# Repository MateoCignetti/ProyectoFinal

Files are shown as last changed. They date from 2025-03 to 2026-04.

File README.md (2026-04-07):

## Repositorio para el proyecto final de la carrera Ingeniería Electrónica. UTN FR San Francisco, 2025.

# Autores
- [ ] Alesandria, Alejo
- [ ] Cignetti, Mateo Antonio
- [ ] Galliano, Ignacio

Shield: [][cc-by-nc-sa]

Esta obra está bajo una
[Licencia Creative Commons Atribución-NoComercial-CompartirIgual 4.0 Internacional][cc-by-nc-sa].

[][cc-by-nc-sa]

[cc-by-nc-sa]: https://creativecommons.org/licenses/by-nc-sa/4.0/deed.es
[cc-by-nc-sa-image]: https://licensebuttons.net/l/by-nc-sa/4.0/88x31.png
[cc-by-nc-sa-shield]: https://img.shields.io/badge/License-CC%20BY--NC--SA%204.0-lightgrey.svg

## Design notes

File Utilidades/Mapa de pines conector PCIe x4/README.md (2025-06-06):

# Tabla de Pines ESP32-S3 para el conector PCIe x4

| Símbolo PCIe x4 | Pad Footprint PCIe x4 | GPIO ESP32-S3 |
|:---:|:---:|:---:|
| HP_Power | 1 | 35 |
| AGND | 7 | GND |
|  3,3Vdc_Signal  | 8 | 3V3 |
| S1 | 9 | 4 (ADC1_3)  |
| S2 | 10 | 5 (ADC1_4)  |
| S3 | 11 | 6 (ADC1_5)  |
| S4 | 12 | 7 (ADC1_6)  |
| S5 | 13 |  15 (ADC2_4)  |
| S6 | 14 |  16 (ADC2_5)  |
| S7 | 15 |  17 (ADC2_6)  |
| S8 | 16 |  18 (ADC2_7)  |
| S9 | 17 | 8 (ADC1_7)  |
| S10 | 18 | 36 |
| S11 | 19 | 37 |
| S12 | 20 | 38 |
| S13 | 21 | 39 |
| S14 | 22 | 40 |
| S15 | 23 | 41 |
| S16 | 24 | 2 (ADC1_1)  |
| MODULE_IDENT  | 25 | 3 (ADC1_0)  |
| HP_Signal | 26 | 42 |

# Imágenes de referencia

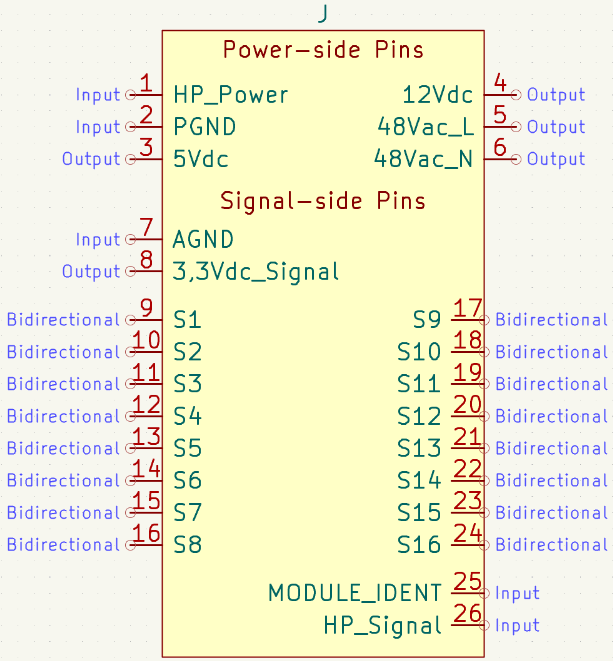
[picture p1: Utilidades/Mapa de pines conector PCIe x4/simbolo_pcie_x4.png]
simbolo-pcie


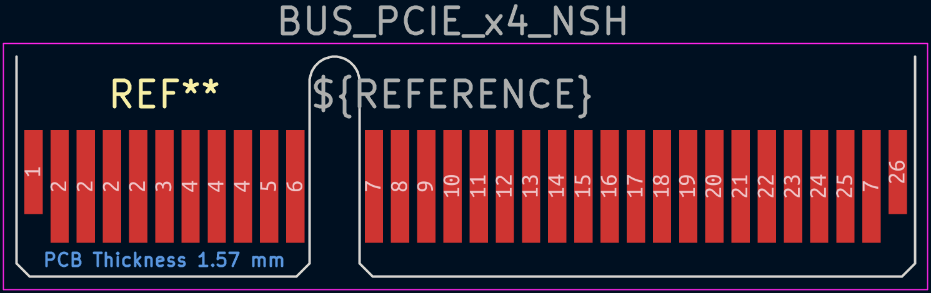
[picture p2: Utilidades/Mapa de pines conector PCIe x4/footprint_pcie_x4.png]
footprint-pcie


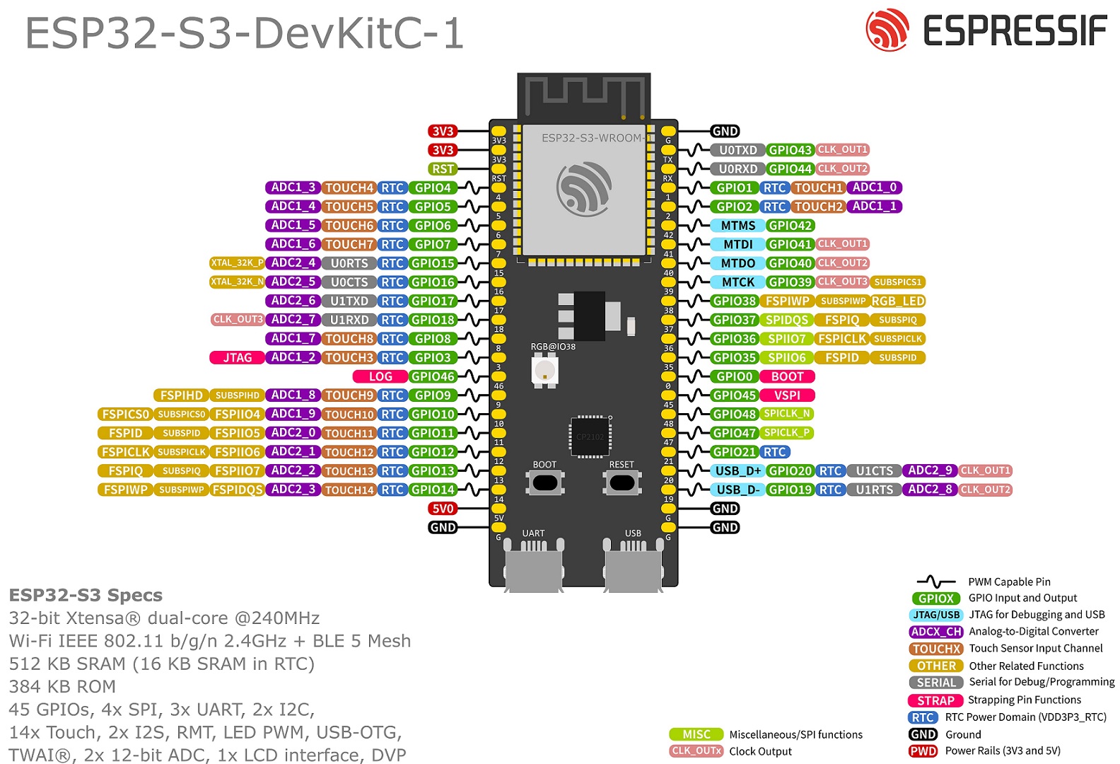
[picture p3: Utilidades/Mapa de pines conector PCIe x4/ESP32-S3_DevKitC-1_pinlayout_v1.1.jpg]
pinout-esp32


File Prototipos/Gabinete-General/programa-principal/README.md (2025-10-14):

| Supported Targets | ESP32-S3 |
| --- | --- |

# General Cabinet - Main Control Program

Modular control system for the General Cabinet project. Automatically detects and manages hot-pluggable power electronics modules.

## Adding New Modules

**Quick Start:** See [MODULE_TEMPLATE.md](MODULE_TEMPLATE.md) for a complete guide.

**Summary:** To add a new module, you only need to:
1. Create `your_module.h` in `modules_include/`
2. Create `your_module.c` in `modules_src/`
3. Edit `module_registry.h` only (add include + list entry)

**Zero changes to core manager code!** See [MODULE_TEMPLATE.md](MODULE_TEMPLATE.md).

(See the README.md file in the upper level 'examples' directory for more information about examples.)

## How to use example

Follow detailed instructions provided specifically for this example.

Select the instructions depending on Espressif chip installed on your development board:

- [ESP32 Getting Started Guide](https://docs.espressif.com/projects/esp-idf/en/stable/get-started/index.html)
- [ESP32-S2 Getting Started Guide](https://docs.espressif.com/projects/esp-idf/en/latest/esp32s2/get-started/index.html)

## Example folder contents

The project **hello_world** contains one source file in C language [hello_world_main.c](main/hello_world_main.c). The file is located in folder [main](main).

ESP-IDF projects are built using CMake. The project build configuration is contained in `CMakeLists.txt` files that provide set of directives and instructions describing the project's source files and targets (executable, library, or both).

Below is short explanation of remaining files in the project folder.

```
├── CMakeLists.txt
├── pytest_hello_world.py      Python script used for automated testing
├── main
│   ├── CMakeLists.txt
│   └── hello_world_main.c
└── README.md                  This is the file you are currently reading
```

For more information on structure and contents of ESP-IDF projects, please refer to Section [Build System](https://docs.espressif.com/projects/esp-idf/en/latest/esp32/api-guides/build-system.html) of the ESP-IDF Programming Guide.

## Troubleshooting

* Program upload failure

    * Hardware connection is not correct: run `idf.py -p PORT monitor`, and reboot your board to see if there are any output logs.
    * The baud rate for downloading is too high: lower your baud rate in the `menuconfig` menu, and try again.

## Technical support and feedback

Please use the following feedback channels:

* For technical queries, go to the [esp32.com](https://esp32.com/) forum
* For a feature request or bug report, create a [GitHub issue](https://github.com/espressif/esp-idf/issues)

We will get back to you as soon as possible.

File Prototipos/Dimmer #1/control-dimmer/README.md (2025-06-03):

# English:
| Supported Targets | ESP32-S3 |
| --- | --- |

## Control for the Dimmer #1 Prototype

This firmware controls the Dimmer #1 prototype using an ESP32-S3 microcontroller. It detects zero crossings of the AC signal and uses two hardware timers to precisely control a TRIAC for phase-cut dimming. The dimming level is set via an analog input (ADC), and all timing is handled without blocking the main program. The code includes optional test signal generation for development without real AC hardware. All configuration and control logic is implemented in `main.c`.

# Español:
| Dispositivos Soportados | ESP32-S3 |
| --- | --- |

## Control para el Prototipo Dimmer #1

Este firmware controla el prototipo Dimmer #1 utilizando un microcontrolador ESP32-S3. Detecta los cruces por cero de la señal de CA y utiliza dos temporizadores de hardware para controlar con precisión un TRIAC mediante atenuación por corte de fase. El nivel de atenuación se ajusta mediante una entrada analógica (ADC), y toda la temporización se gestiona sin bloquear el programa principal. El código incluye la generación opcional de señales de prueba para el desarrollo sin hardware de CA real. Toda la configuración y lógica de control está implementada en `main.c`.

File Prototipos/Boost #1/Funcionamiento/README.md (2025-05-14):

# Convertidor Boost

Circuito genérico del convertidor Boost

### Lista de Entradas-Salidas

<!-- 
| Señal | Tipo |
|----|-----|
| Tensión de alimentación | Entrada |
| Señal de control gate | Entrada |
| Tensión de salida | Salida |
| Tensión de retroalimentación | Salida |
-->

| Entrada | Salida |
|----|-----|
| Tensión de alimentación, $V_{cc}$ = 12 V | Tensión de salida, $V_{out}$ = 24 V|
| Señal de control gate, PWM -- 0 a 3,3 V | Tensión de retroalimentación, $V_\beta$ entre 0 y 3,3 V  |

El desarrollo siguiente fue obtenido de, [Electrical Technology](https://www.electricaltechnology.org/2020/09/buck-converter.html), 

## Resumen
Un convertidor boost, también conocido como elevador de voltaje, es un tipo de convertidor DC-DC que incrementa la tensión de entrada a un nivel superior en la salida. Funciona almacenando energía en un inductor durante el tiempo en que un interruptor (generalmente un transistor) está cerrado, y transfiriéndola a través de un diodo hacia la carga cuando el interruptor se abre. 

Este aumento de tensión en la salida se consigue a expensas de una menor corriente de salida. Aunque esto depende del diseño específico, es común que la corriente disminuya al elevar el voltaje, de manera de conservar la potencia según el principio de conservación de la energía.
<!--
FALTA HACER RESUMEN
-->

## Funcionamiento

### Componentes principales del convertidor

* Interruptor, puede ser un transistor BJT como un MOSFET.
* Diodo de rectificación.
* Inductor.
* Capacitor de salida.
* Controlador PWM.

### Modo Encendido

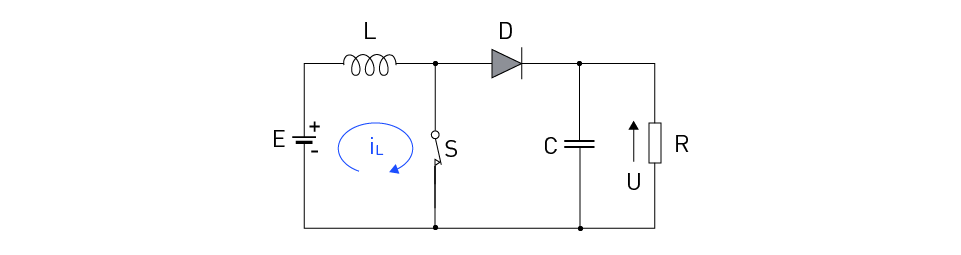
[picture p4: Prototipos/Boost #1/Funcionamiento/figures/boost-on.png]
Modo 1


Durante esta etapa, el voltaje de entrada es aplicado al inductor, generando que acumule energía. El diodo se encuentra polarizado inversamente debido a que el nodo que se encuentra entre el inductor, interruptor y el diodo, se encuentra a un potencial prácticamente de 0, por ello la corriente se deriva por el interruptor y no por el diodo, además hay que considerar que en esta etapa, el capacitor de salida se encuentra suministrando energía a la carga, por ende el cátodo del diodo se encuentra a un potencial mayor que el ánodo del mismo, por eso se dice que está polarizado de forma inversa.

### Modo Apagado

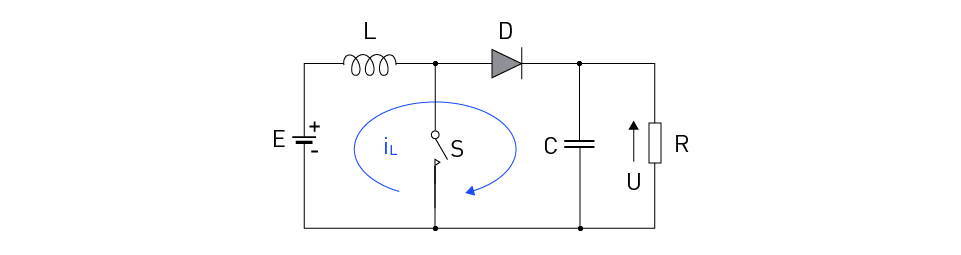
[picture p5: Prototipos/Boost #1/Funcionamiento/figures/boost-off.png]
Modo 2


Cuando el interruptor se abre, toda la energía almacenada en el inductor es aplicada en el diodo haciendo que el mismo se polarice directamente, produciendo que el inductor disminuya la energía almacenada en el mismo. 

### Medición de tensión

La medición de tensión se realiza de la misma forma que en el caso del convertidor Buck, en caso de ser necesario una mayor explicación retomar el documento, FUNCIONAMIENTO DEL BUCK

Si el interruptor tiene un período de conmutación lo suficientemente rápido, el inductor no llega a descargase en su totalidad entre los períodos, haciendo que en la carga se aplique un voltaje mayor al voltaje de entrada. También, mientras el interruptor está abierto, el capacitor de salida se carga con este voltaje combinado. Cuando el interruptor se cierra, el capacitor de salida es el encargado de suministrar energía a la carga. Por ello el interruptor debe ser rápidamente conmutado a abierto para evitar la descarga completa del capacitor de salida.

$V_{out} = \frac{V_{in}}{1-D}$

La ecuación anterior muestra el voltaje en régimen permanente, y como al aumentar el duty, la tensión de salida se ve aumentada.

### Modo continuo y descontinuo de conducción

**Modo Continuo de conducción**

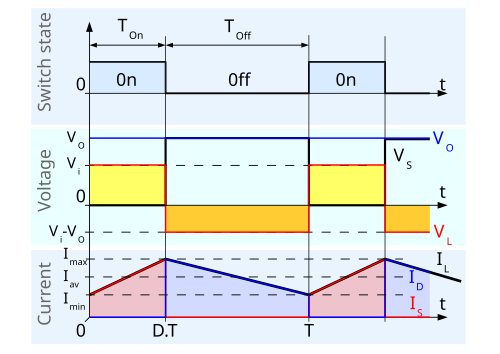
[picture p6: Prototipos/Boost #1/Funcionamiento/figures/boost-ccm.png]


**Modo Discontinuo de conducción**

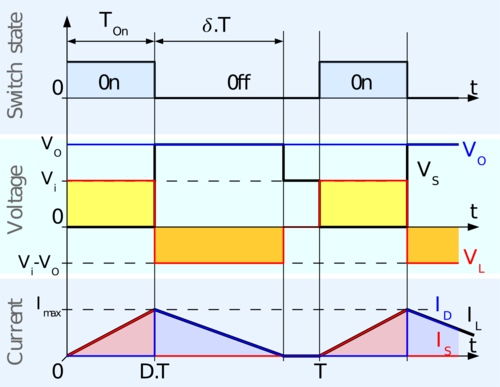
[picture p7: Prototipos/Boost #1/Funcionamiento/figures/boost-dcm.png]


Para cargas ligeras, el convertidor trabaja en modo Discontinuo.

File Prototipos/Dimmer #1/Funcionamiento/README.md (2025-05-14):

# Recortador de onda "Dimmer"

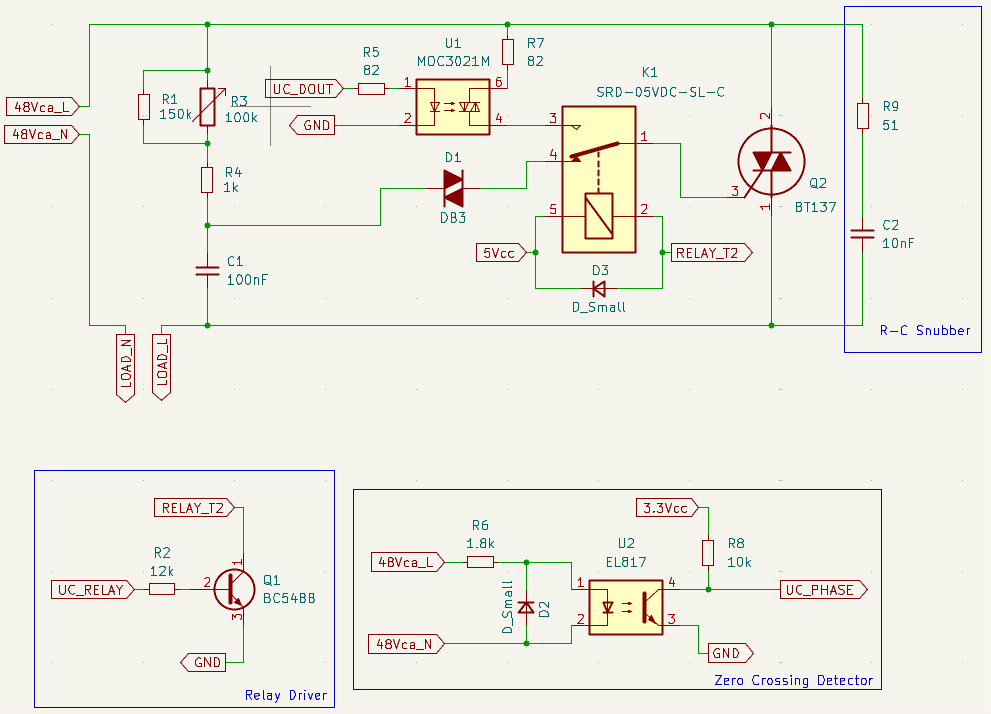
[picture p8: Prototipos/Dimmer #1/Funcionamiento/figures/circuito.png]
Circuito de placa Dimmer


## Entradas y salidas
| Entrada | Salida |
|--- |--- |
|$V_{ca}$ = 48 Vca | $UC_{phase}$ = Onda cuadrada 3.3 Vcc  |
|$5V_{cc}$ = 5 Vcc | $Load$ = Onda recortada 0-48 Vca RMS  |
|$3.3V_{cc}$ = 3.3 Vcc | |
|$UC_{Dout}$ = Pulso 3.3 Vcc | |
|$UC_{Relay}$ = 0 V o 3.3 Vcc | |

## Resumen

El recortador de onda "Dimmer" tiene como objetivo regular la potencia
entregada a la carga, mediante el uso de un tiristor, recortando la onda
de tensión aplicada a la carga. En esta placa, se utilizan dos métodos
distintos de control: analógico y digital.

El control analógico permite cambiar el ángulo de disparo del tiristor TRIAC. Con un simple circuito R-C, se varía la resistencia y, por lo tanto, la constante de tiempo de carga del capacitor para retardar el disparo del DIAC, encargado de disparar el TRIAC. Debido al comportamiento del TRIAC, una vez "disparado", no deja de conducir hasta el cruce por cero de la tensión aplicada entre ambos ánodos.

El control digital se compone de dos circuitos distintos: el Zero Crossing Detector (detector de cruce por cero) y el driver de TRIAC. El primero permite al microcontrolador sincronizarse con la tensión de corriente alterna y el segundo permite al microcontrolador "disparar" el TRIAC cuando se quiera.

Con un circuito driver de Relé, se permite cambiar entre ambos modos, siendo el control analógico el activado por defecto (contacto normal-cerrado).

## Control de fase con tiristores

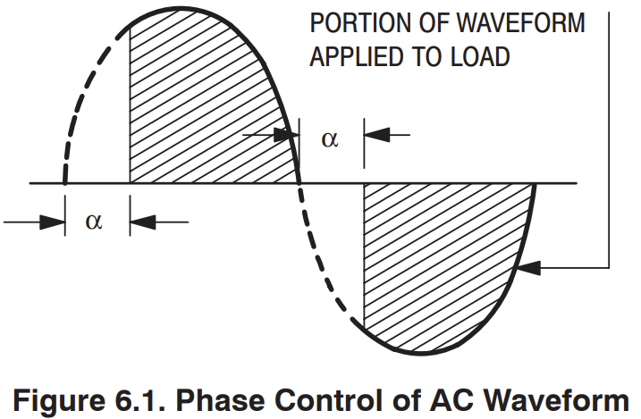
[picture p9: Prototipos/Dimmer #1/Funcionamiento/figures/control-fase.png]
Control de fase


El método más común de control electrónico de potencia de CA se denomina control de fase. La Figura 6.1 ilustra este concepto. Durante la primera parte de cada semiciclo de la onda sinusoidal de CA, se abre un interruptor electrónico para impedir el flujo de corriente. En un ángulo de fase específico $\alpha$, este interruptor se cierra para permitir que se aplique toda la tensión de línea a la carga durante el resto de ese semiciclo. La variación de $\alpha$ controlará la parte de la onda sinusoidal total que se aplica a la carga (área sombreada) y, por lo tanto, regulará el flujo de potencia hacia la carga.

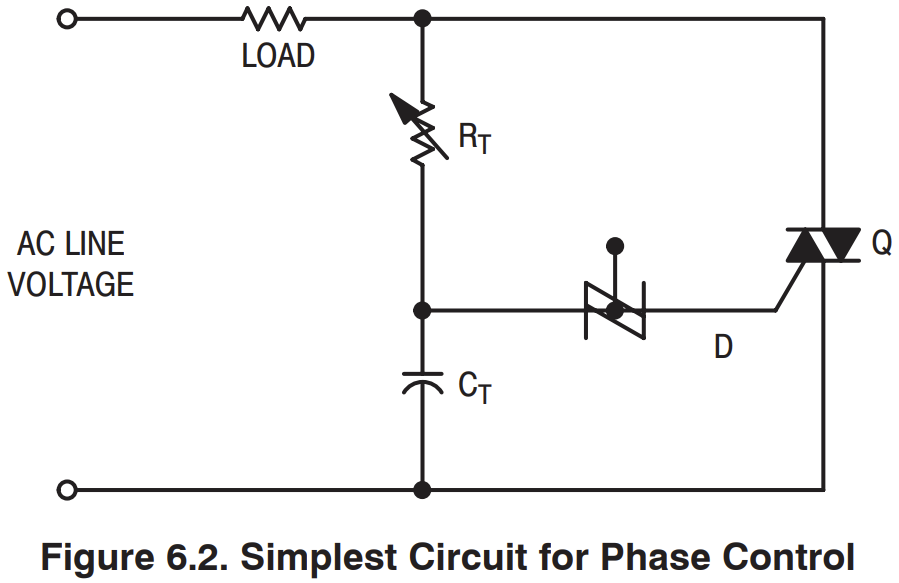
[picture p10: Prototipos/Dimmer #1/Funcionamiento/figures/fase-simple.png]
Circuito básico de control de fase


El circuito más simple para lograr el control de fase se muestra en la Figura 6.2. En este caso, el interruptor electrónico es un TRIAC (Q) que se activa mediante un pequeño pulso de corriente en su compuerta. El TRIAC se desactiva automáticamente cuando la corriente que lo atraviesa pasa por cero. En el circuito mostrado, el capacitor CT se carga durante cada semiciclo mediante la corriente que fluye a través de la resistencia RT y la carga. El hecho de que la carga esté en serie con RT durante esta parte del ciclo tiene poca importancia, ya que la resistencia de RT es mucho mayor que la de la carga. Cuando la tensión en el CT alcanza la tensión de ruptura del disparador bilateral DIAC (D), se libera la energía almacenada en el capacitor CT. Esta energía produce un pulso de corriente en el DIAC, que fluye a través de la compuerta del TRIAC y lo activa. Dado que tanto el DIAC como el TRIAC son dispositivos bidireccionales, los valores de RT y CT determinarán el ángulo de fase en el que se activará el TRIAC en los semiciclos positivo y negativo de la onda sinusoidal de CA.

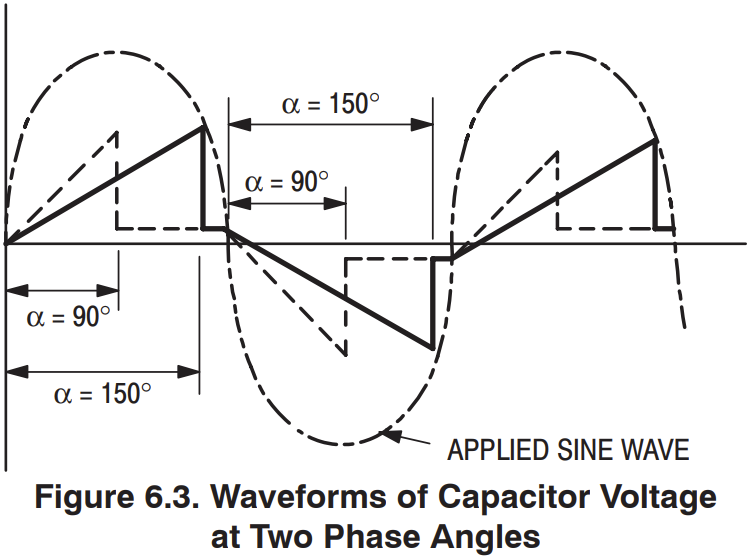
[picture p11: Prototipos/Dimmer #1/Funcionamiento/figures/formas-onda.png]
Formas de onda de tensión de capacitor


La forma de onda del voltaje a través del capacitor para dos condiciones de control típicas ($\alpha$ = 90° y 150°) se muestra en la Figura 6.3. Si se utiliza un rectificador controlado por silicio en este circuito en lugar del TRIAC, solo se controlará un semiciclo de la forma de onda. El otro semiciclo se bloqueará, lo que genera una salida de CC pulsante cuyo valor promedio puede variarse ajustando el RT. 
(Referencia: [Thyristor Theory and Design Considerations: Handbook](https://www.rsp-italy.it/Electronics/Databooks/ON/_contents/ON%20Thyristor%20theory%20and%20design%20handbook%20HBD855D%202005.pdf))

Este tipo de control de fase se recomienda solamente para circuitos con carga resistiva o levemente inductiva (ver [AN308 (STMicroelectronics)](https://www.st.com/resource/en/application_note/an308-triac-analog-control-circuits-for-inductive-loads-stmicroelectronics.pdf))

## Circuito detector de cruce por cero (ZCD)

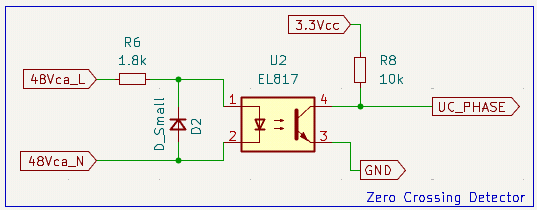
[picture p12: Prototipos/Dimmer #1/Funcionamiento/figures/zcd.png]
Circuito ZCD


Este simple circuito convierte la señal de entrada de CA sinusoidal en una señal aislada cuadrada, que permite al microcontrolador conocer el momento de cruce por cero (cuando la onda cuadrada pasa de 3,3 V a 0 V o 0 V a 3,3 V).

En el semiciclo positivo de la tensión de CA, se enciende el led interno del optoacoplador, lo que polariza el transistor de salida, que lleva la tensión UC_PHASE a 0 V. En el semiciclo negativo, la corriente fluye por el diodo D2, manteniendo la tensión reversa del led interno fija y menor a la máxima permitida (6 V para el EL817).

## Driver de TRIAC

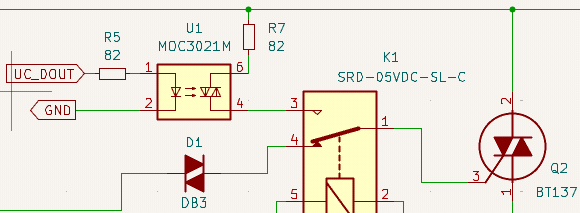
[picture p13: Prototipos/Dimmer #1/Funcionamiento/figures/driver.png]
Driver TRIAC


Con este circuito se permite disparar el TRIAC en cualquier momento de forma aislada, solamente enviando un pulso con el microcontrolador a UC_DOUT. No es necesario mantener la señal por más que unos pocos microsegundos, ya que una vez disparado el TRIAC, no deja de conducir hasta que la tensión aplicada entre ambos ánodos cruza por cero.

## Driver de relé

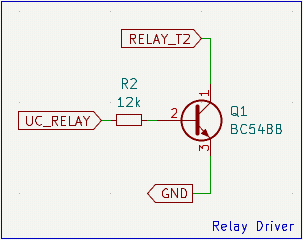
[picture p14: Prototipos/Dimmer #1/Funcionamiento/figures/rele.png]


Simple circuito que permite conmutar el relé, para así cambiar entre ambos modos de control (analógico y digital). Cuando UC_RELAY es de 0 V, el circuito utilizado es el de control analógico, mientras que cuando UC_RELAY es de 3,3 V, se activa el control digital.

## Red Snubber

Es imperativo implementar algún método para restringir la tasa de aumento de la tensión reaplicada del triac a un valor que permita la desactivación del triac en condiciones de carga inductiva. Un método comúnmente aceptado para mantener la dv/dt de conmutación dentro de niveles tolerables es utilizar una red Snubber RC en paralelo con los terminales principales del triac. Dado que la tasa de aumento de la tensión aplicada en los terminales del triac depende de la impedancia de carga y de la red Snubber RC, el circuito puede evaluarse en las peores condiciones de temperatura de funcionamiento y corriente principal máxima. Los valores de resistencia y capacitancia en red Snubber se ajustan entonces para que la tasa de aumento de la tensión dv/dt de conmutación se encuentre dentro del límite mínimo especificado en cualquiera de las condiciones mencionadas anteriormente. El valor de la resistencia del Snubber debe ser lo suficientemente alto como para limitar las corrientes de descarga de la capacitancia del Snubber durante el encendido y amortiguar la oscilación del LC durante la conmutación. Generalmente, se prefiere la combinación de valores de Snubber con la mayor resistencia y la menor capacitancia que proporcione un funcionamiento satisfactorio. (Referencia: [Thyristor Theory and Design Considerations: Handbook](https://www.rsp-italy.it/Electronics/Databooks/ON/_contents/ON%20Thyristor%20theory%20and%20design%20handbook%20HBD855D%202005.pdf))

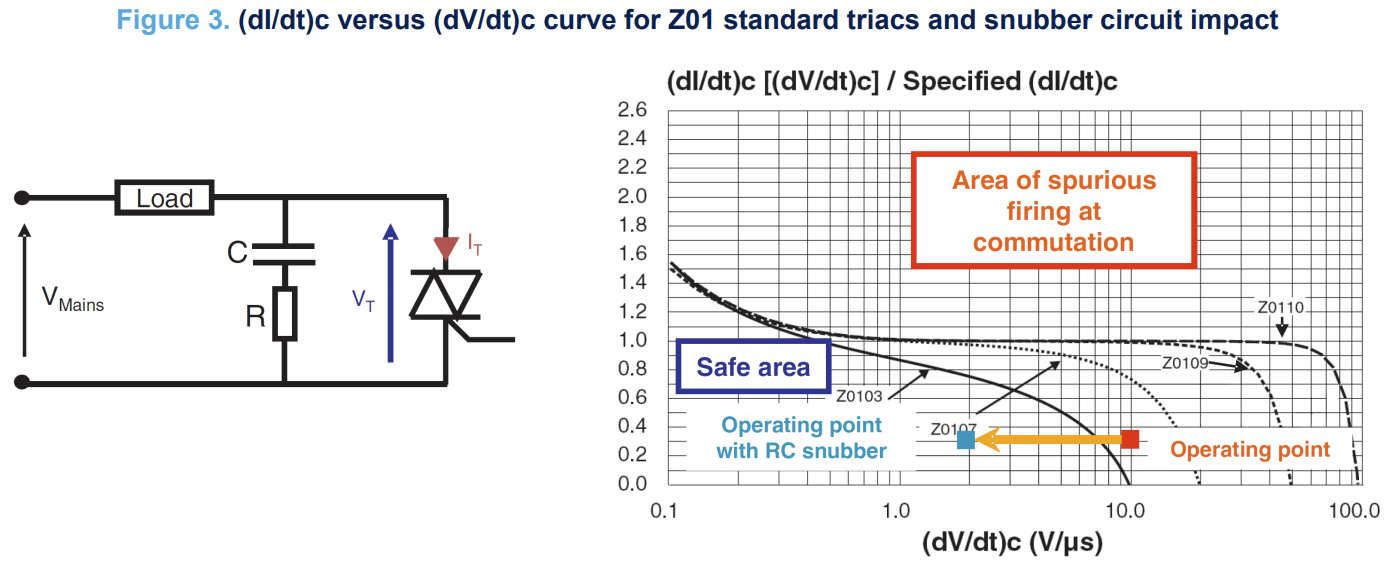
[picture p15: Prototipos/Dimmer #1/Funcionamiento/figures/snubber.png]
Red Snubber


Como se observa en la figura 3, un alto dv/dt puede causar un falso disparo del TRIAC, afectando negativamente al circuito control de fase. (Más info, ver [AN437 STMicroelectronics](https://www.st.com/resource/en/application_note/an437-rc-snubber-circuit-design-for-triacs-stmicroelectronics.pdf))

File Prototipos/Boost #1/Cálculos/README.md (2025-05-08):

# Diseño de Convertidor Boost

Circuito Boost

### Requisitos

| Entrada | Salida |
|- |- |
|$V_{in}$ = 12 V |$V_{out}$ = 24 V |
|$I_{in}$ = 1 A |$I_{out}$ = 0,5 A  |

El diseño del convertidor fue realizado siguiendo el siguiente documento, [Texas Instruments](https://www.ti.com/lit/an/slva372d/slva372d.pdf?ts=1743949048852)

**Criterios de diseño del circuito**

* $R_{load} = \frac{24 V}{0,5 A} = 48 \Omega$
* Ripple,
  * $\Delta I_L = I_{in} * 0,3 = 1  A * 0,3 = 0,3 \ A$
  * $\Delta V_{out} = V_{out} * 0,05 = 1,2 \ V$
* Frecuencia de conmutación, 15 kHz.

## Cálculo del Duty Cycle máximo

$$D = 1 - \frac{V_{in} * \eta }{V_{out}} = 1 - \frac{12 * 0,8 }{24} = 0,6$$

## Cálculo de Inductor

$$L = \frac{V_{in} * (V_{out} - V_{in})}{\Delta I_L * f_s * V_{out}} = \frac{12V * (24V - 12V)}{0,3A * 15 \times 10^3 Hz * 24V} = 1,33 mH$$

Tal vez sea conveniente la elección de un inductor arbitrario y luego calcular el ripple producto del mismo. Se deja como inquietud para las pruebas prácticas. Este valor se verá afectado en función de la fuente que se utilice para alimentación, 1 A tal vez es poca corriente. Si la corriente de entrada es de 2 A, el inductor se reduce a la mitad 666,66 uH

## Selección de Capacitor de entrada

Utilizado para filtrar la tensión de entrada, si la fuente es demasiado ruidosa, el capacitor se puede incrementar para mejorar el filtrado. 

Valor elegido, $1 \ \mu F$. Requerirá ajustes en la práctica.

## Cálculo de Capacitor de salida

$$C_{out} = \frac{I_{out} * D}{f_s * \Delta V_{out}} = \frac{0,5 A * 0,6}{15 \times 10^3 Hz * 1,2 V} = 16,67 \ \mu F$$

## Cálculo de corriente por el diodo

$$I_D = I_{out_{max}}$$

Se recomienda el uso de diodos Schottky.

## Red de realimentación

$$V_{out} = \frac{V_{in}*R_2}{R_1+R_2}$$

$$3,3 V= \frac{24 V * 4,7 k\Omega}{R_1 + 4,7 k\Omega}$$

$$R_1 = 29,48 k\Omega \approx 27 k\Omega + 2,2 k\Omega$$

## Cálculo red Snubber transistor de conmutación

Para más detalles sobre el cálculo revisar, [Cáculos Buck](https://github.com/MateoCignetti/ProyectoFinal/tree/main/Prototipos/Buck%20%231/C%C3%A1lculos). Además los transistores utilizados como driver son los mismos, por ende la red de Snubber también lo es (se tendrá que comprobar en la práctica).

Se supone un valor de inductancia parásita típico de 50 nH. $C_P = C_{OSS}$

* IRFZ44N

$C_{OSS} = 330 pF = C_{snub_{min}}$

$$f_{ring} = \frac{1}{2 \pi * \sqrt{L_P * C_P}} = \frac{1}{2 \pi * \sqrt{50 \ nH * 330 \ pF}} = 39,18 \ MHz$$

$$ R_{snub} = \frac{1}{2\pi f_{ring} C_{snub}} = 12,31 \ \Omega$$

## Filtro RC para entrada de ADC

$f_c = 100 Hz$

$C = 1 \ \mu F$

$f_c = \frac{1}{2\pi * R * C}$

$$R = \frac{1}{2\pi * f_c * C} = 1591 \ \Omega \approx 1,5  \ k\Omega$$

## Diseño Prototipo Boost 12 V a 24 V

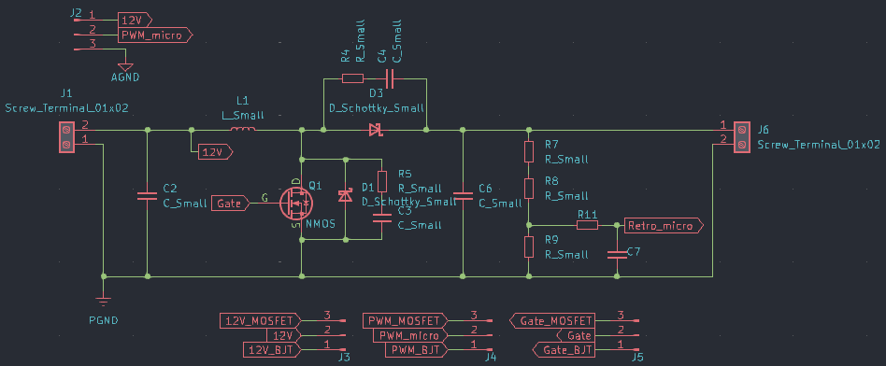
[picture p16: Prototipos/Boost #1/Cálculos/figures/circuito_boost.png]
Circuito Boost

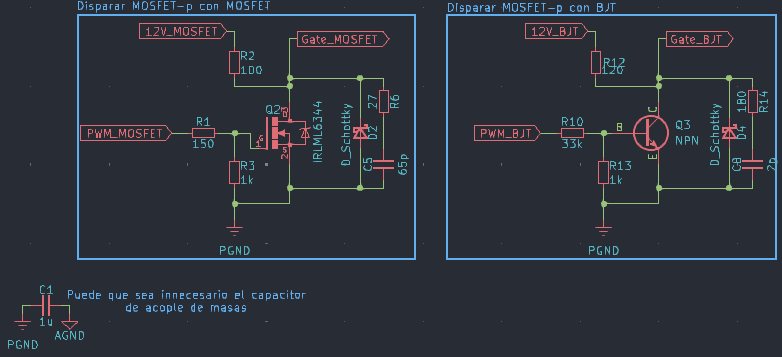
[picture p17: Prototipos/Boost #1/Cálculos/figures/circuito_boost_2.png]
Circuito Boost


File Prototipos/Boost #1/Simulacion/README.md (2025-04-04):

# Resultados de Simulación

## Circuito Convertidor Boost

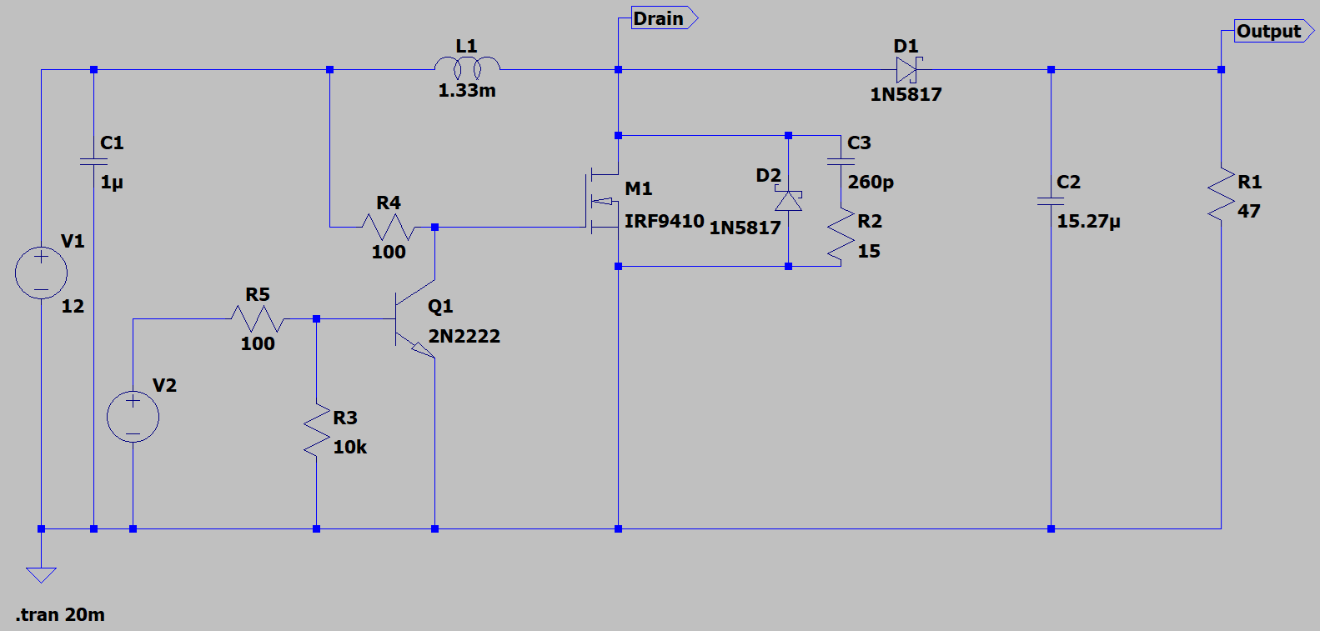
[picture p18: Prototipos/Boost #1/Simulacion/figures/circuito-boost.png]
Convertidor Boost


### Tensión de Salida del convertidor

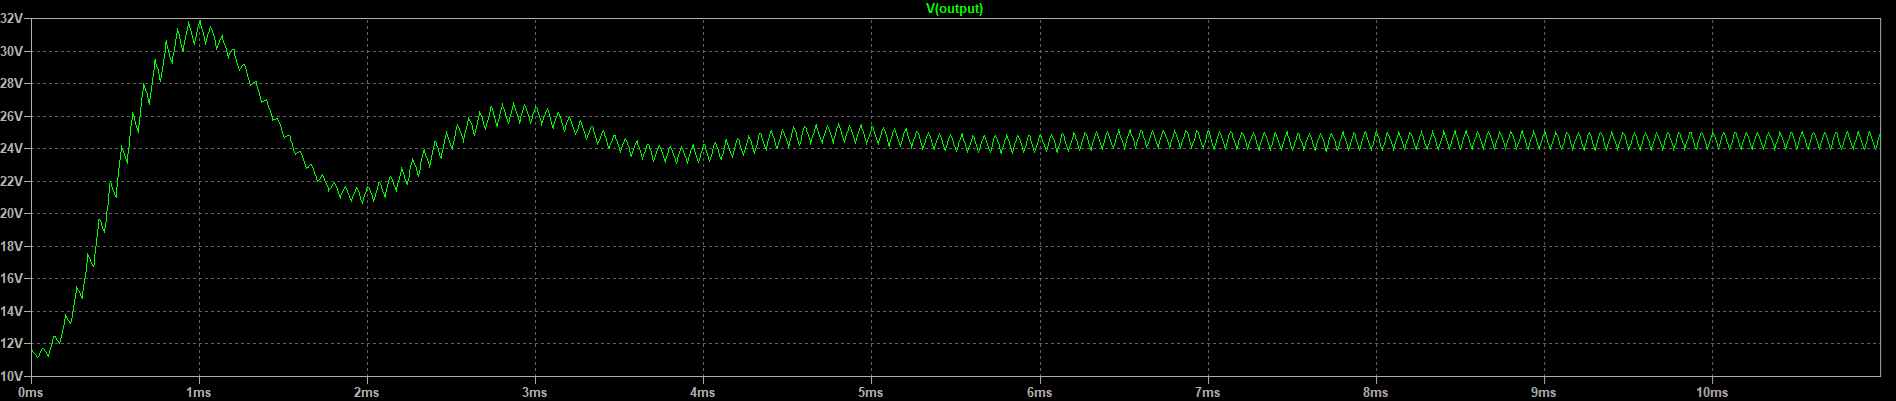
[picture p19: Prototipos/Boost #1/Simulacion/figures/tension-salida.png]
Convertidor Boost


La tensión de salida de convertidor presenta una respuesta subamortiguada por la naturaleza de un sistema
de segundo orden. Para mejorar la respuesta del convertidor es necesario un sistema de control sencillo, como
puede ser un PI.

### Modo CCM

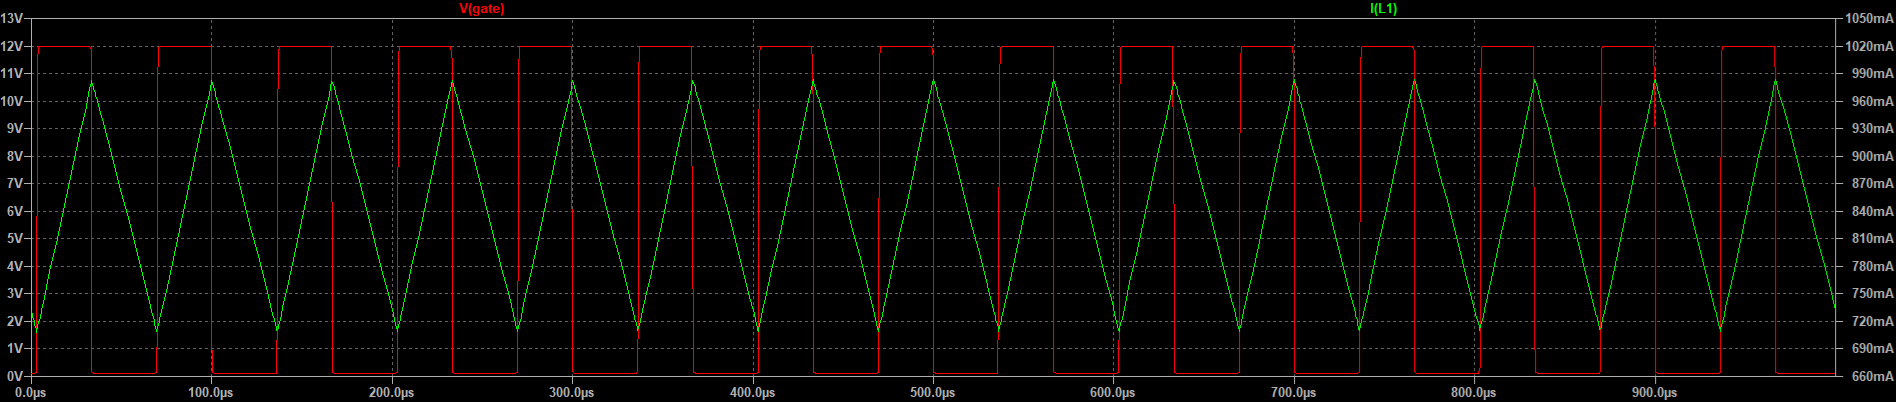
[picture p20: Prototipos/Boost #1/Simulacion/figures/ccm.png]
Convertidor Boost


La corriente en el inductor nunca llega a ser '0' por ello se lo denomina modo continuo de conducción. 
Suele ser necesario cuando la carga requiere más corriente.

Pruebas con carga de 47 $\Omega$ y un duty de 44 %

### Modo DCM

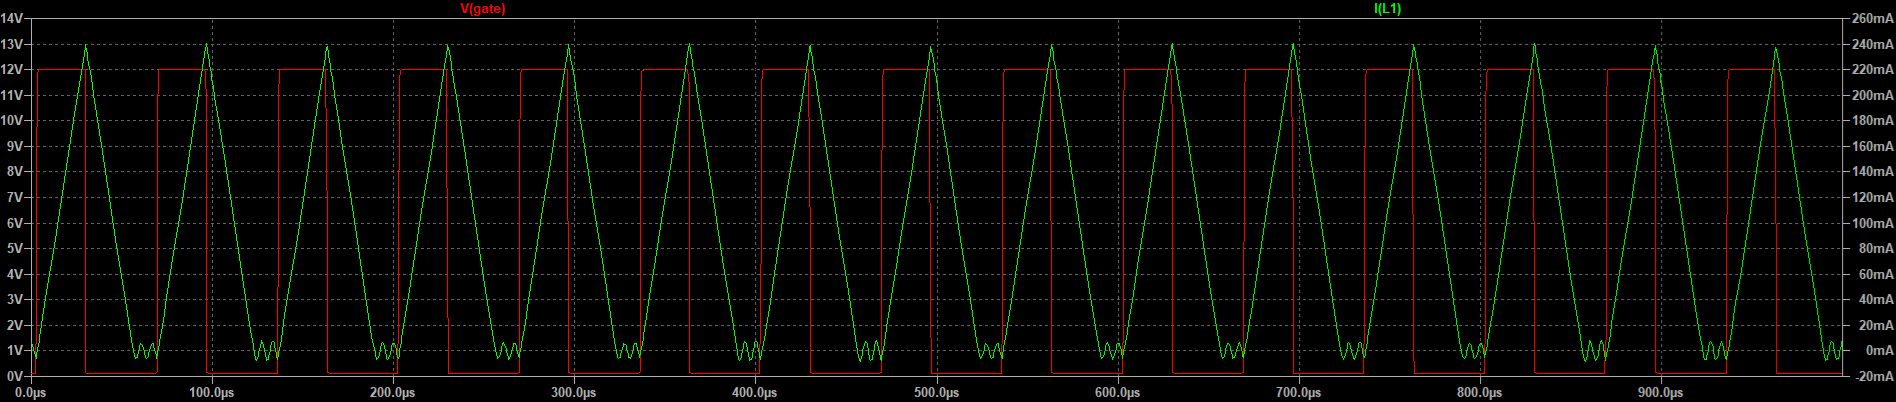
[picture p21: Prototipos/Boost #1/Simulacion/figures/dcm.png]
Convertidor Boost


En este caso, a diferencia del CCM, la corriente en el inductor es '0' antes de que el transistor de conmutación se encienda nuevamente. Este modo se lo conoce como modo discontinuo de conducción. Se aplica
cuando la carga no tiene un consumo excesivo.

Pruebas con carga de 400 $\Omega$ y un duty de 39 %

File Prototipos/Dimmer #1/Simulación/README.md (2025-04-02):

# Resultados simulación

## Circuito
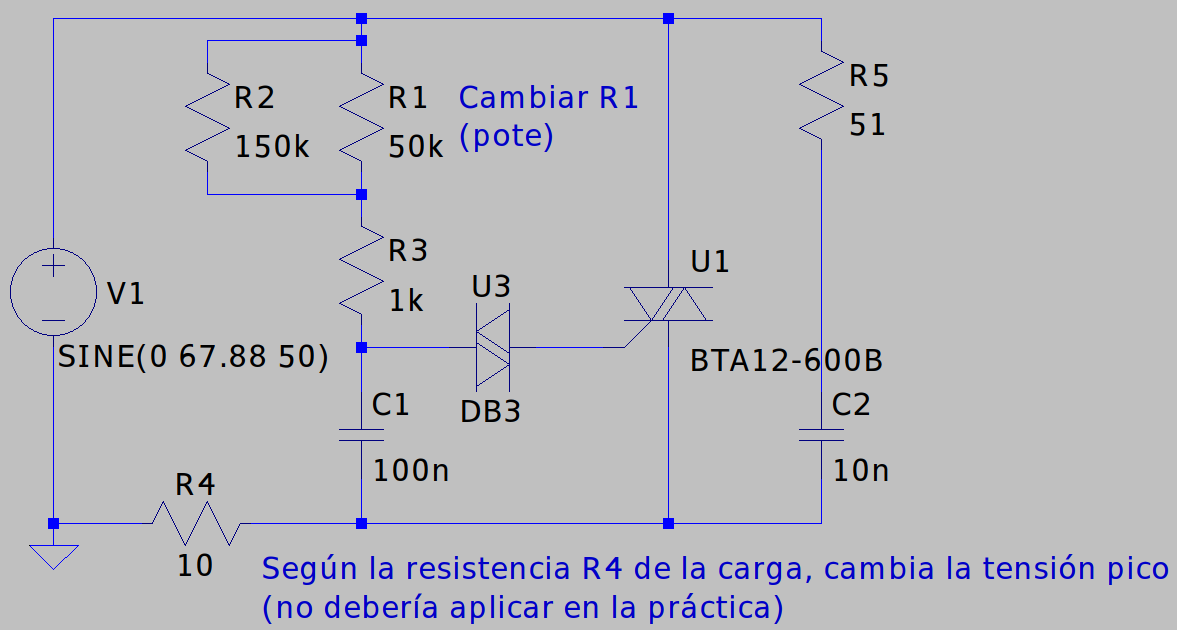
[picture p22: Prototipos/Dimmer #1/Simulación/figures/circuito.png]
Circuito


## Formas de onda
- 🔵 Tensión de entrada
- 🟢 Tensión en la carga

(La amplitud varía según el valor de la resistencia de la carga, en la práctica no debería afectar)

### Potenciómetro en 0
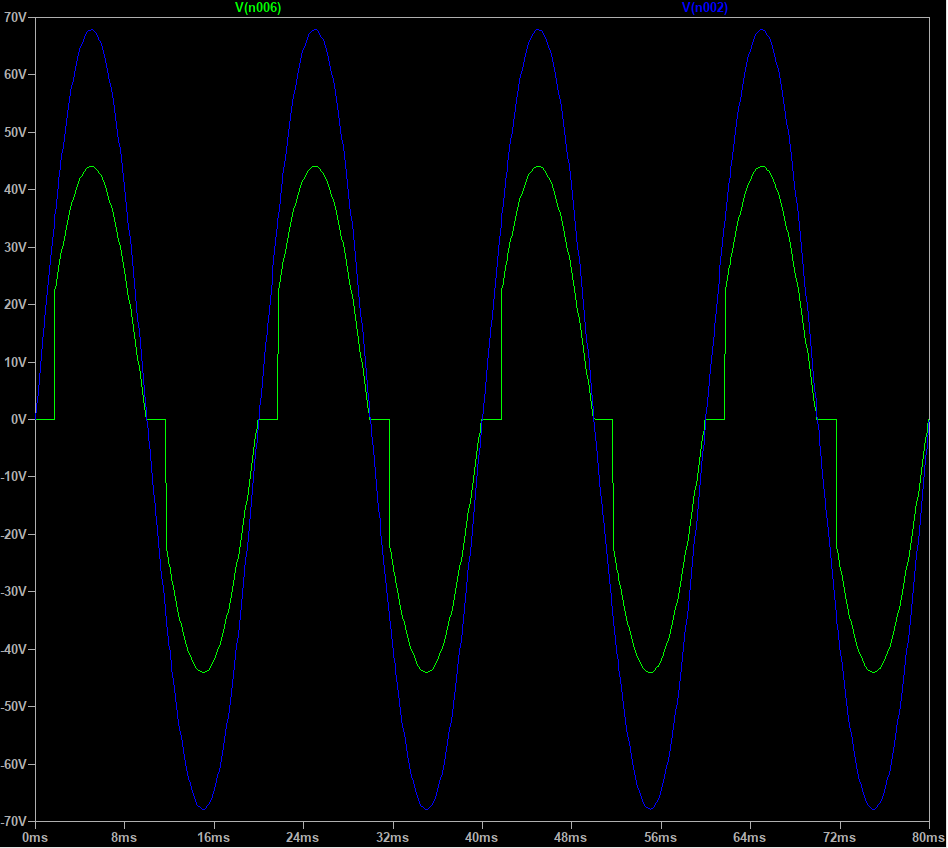
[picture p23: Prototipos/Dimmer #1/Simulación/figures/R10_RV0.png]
Pote0


### Potenciómetro en 50k (50%)
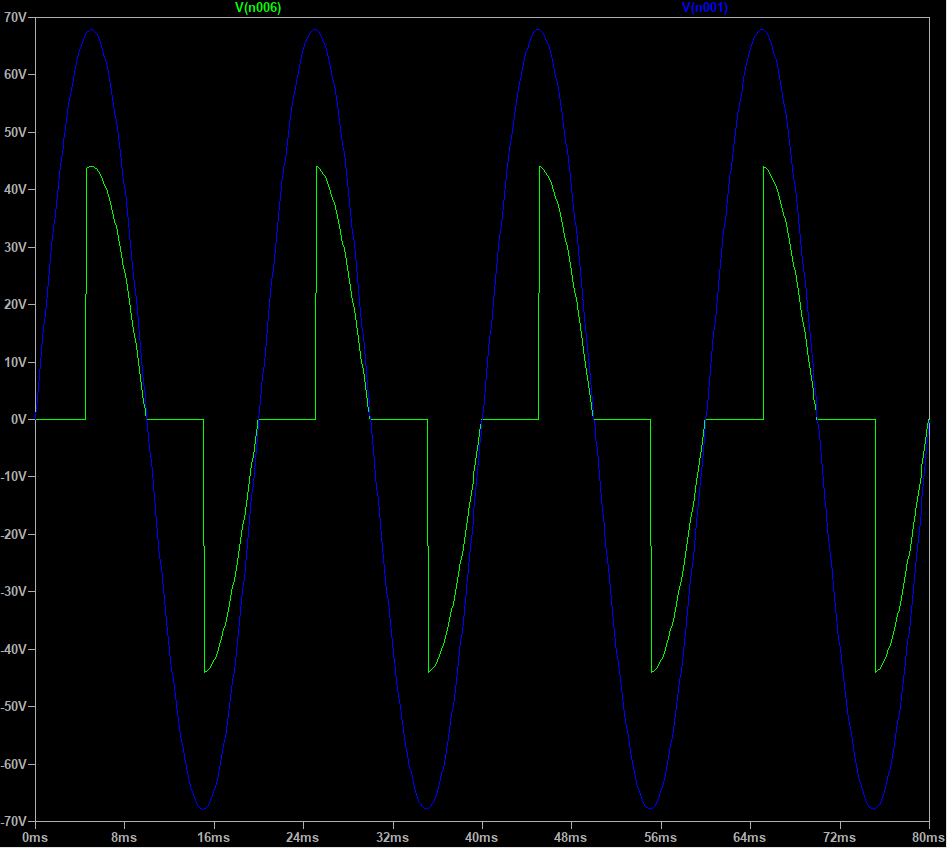
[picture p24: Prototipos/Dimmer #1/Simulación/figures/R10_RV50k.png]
Pote50


### Potenciómetro en 100k (100%)
Pote100

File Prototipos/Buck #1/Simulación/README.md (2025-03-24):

### Resultados

Circuito Simulado

Señal Entrada y Salida

Señal Gate y drenador

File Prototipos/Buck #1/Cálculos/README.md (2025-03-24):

# Diseño Convertidor Buck

Buck

### Requisitos
| Entrada | Salida |
|---|---|
|$V_{in}$ = 12 V| $V_{out}$ = 6 V|
|$I_{in}$ = 1 A | $I_{out}$ = 2 A|
|P = 12 W|

Para el diseño se siguió un diseño de referencia de
[Texas Instrumens](https://www.ti.com/lit/an/slva477b/slva477b.pdf?ts=1740493656949).

#### Criterios de diseño
* R = 1,5 $\Omega$
* Ripple
  * $\Delta V_{out} = 0,02 \ V_{out} = 0,02 * 6 V = 0,12 \ V$ 
  * $\Delta I_L = 0,3 \ I_{out} = 0,3 * 2 A = 0,6 \ A$
* Frecuencia de conmutación ($f_s$), 15 kHz

### Cálculo de Duty Cycle máximo

$$D_{max} = \frac{V_{out}}{V_{in} * \eta} = \frac{6 V}{12 V * 0,9} = 0,55$$

Se determina un rendimiento teórico del 90%, se lo toma como criterio de diseño.

### Cálculo de capacitor de salida

$$C_{min} = \frac{\Delta I_L}{8 * f_s * \Delta V_{out}} = \frac{0,6 A}{8*15\times10^3 Hz * 0,12 V} = 41,66 \ \mu F$$

Se recomienda el uso de capacitores cerámicos de bajo ESR con material dieléctrico
X5R. Cualquier capacidad mayor a la calculada puede ser utilizada, sin perder el funcionamiento 
del convertidor.

### Cálculo de inductor

$$L = \frac{(V_{in}-V_{out})*D_{max}}{f_s * \Delta I_L} = \frac{(12 V-6 V)*0,55}{15\times10^3 Hz * 0,6 A} = 366,66 \ \mu H$$

### Cálculo diodo

$$I_D = I_{out} *(1-D) = 2 \ A * (1-0.55) = 0,9 \ A$$

Corriente media aplicada en el diodo de rectificación. Se recomienda utilizar un Schottky, la 
tensión soportada por el diodo debe ser al menos un 30% más que la tensión de salida del convertidor

### Red Snubber 

Para este cálculo se utilizó el siguiente documento [Toshiba](https://toshiba.semicon-storage.com/info/application_note_en_20180901_AKX00078.pdf?did=63595).
No se pudo seguir por completo, pero se realizaron algunas consideraciones para el cálculo.

Se supone un valor de inductancia parásita típico de 50 nH. $C_P = C_{OSS}$

+ IRF9540

$C_{OSS} = 400 \ pF \approx C_{snub}(min)$

$$f_{ring} = \frac{1}{2 \pi * \sqrt{L_P * C_P}} = \frac{1}{2 \pi * \sqrt{50 \ nH * 400 \ pF}} = 35,6 MHz$$

$$ R_{snub} = \frac{1}{2\pi f_{ring} C_{snub}} = 11,2 \ \Omega$$

$f_{ring}$, representa la frecuencia de las oscilaciones existentes en la conmutación del transistor, no se
tiene este valor, pero se calcula en función de un valor estimado de Inductancia parásita, lo ideal es
medirlo uno vez el circuito se encuentre armado.

+ IRLML6344

$C_{OSS} = 65 \ pF \approx C_{snub}(min)$

$$f_{ring} = \frac{1}{2 \pi * \sqrt{L_P * C_P}} = \frac{1}{2 \pi * \sqrt{50 \ nH * 65 \ pF}} = 88,3 MHz$$

$$ R_{snub} = \frac{1}{2\pi f_{ring} C_{snub}} = 27,7 \ \Omega$$

**Puede ser necesario una red de snubber para el diodo rectificador**

### Filtro RC para entrada de ADC

$f_c = 100 Hz$

$C = 10 \ \mu F$

$f_c = \frac{1}{2\pi * R * C}$

$$R = \frac{1}{2\pi * f_c * C} = 159.15 \ \Omega \approx 150 \ \Omega$$

### Divisor de tensión (retroalimentación micro)

Tensión de salida requerida 3,3 V.

Divisor tensión

$$V_{out} = \frac{V_{in}*R_2}{R_1+R_2}$$

$$3,3 \ V= \frac{12 \ V*4,7 \ k\Omega}{R_1+4,7 \ k\Omega}$$

$$R_1 = 12,39 \ k\Omega$$

### Resistencia limitadora de corriente para carga de capacitancia de gate de transistor utilizado como driver

Microcontrolador a utilizar ESP32-S3, según la hoja de datos la corriente acumulada de todos los pines
es de 1,5 A. [Datasheet](https://www.espressif.com/sites/default/files/documentation/esp32-s3_datasheet_en.pdf), como posee 45 GPIOS, el resultado aproximado de corriente por pin es de 33,33 mA.

$$R_{min} = \frac{V}{I} = \frac{3,3 \ V}{33,33 mA} = 99 \Omega$$

Se elige una resistencia de 150 $\Omega$. Esta resistencia es necesaria porque el microcontrolador
vería un cortocircuito cuando el capacitor de entrada está descargado generando una alta corriente,
además ayuda a prevenir corrientes residuales de oscilación. A tener en cuenta, cuanto mayor es el valor
de resistencia, la respuesta del transistor disminuye.

[Infineon](https://www.infineon.com/dgdl/Infineon-power_mosfet_basics-Article-v01_00-EN.pdf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), página 11

[Stack Exchange](https://electronics.stackexchange.com/questions/287792/what-the-best-way-to-calculate-rg-gate-driver-for-mosfet)

[Texas Instruments](https://www.ti.com/lit/ml/slua618a/slua618a.pdf?ts=1741669157446)

Tener en cuenta que el transistor utilizado es un MOSFET de nivel lógico, se puede utilizar un transistor BJT en caso de que la primer solución no entregue resultados acordes a lo esperado. Una opción en transistores BJT es el uso de 2N2222, BC548,  2N2219. IRL540 (MOSFET)

### Resistencia para transistor de conmutación

La corriente requerida para cargar la gate del transistor está determinada por su capacitancia de gate, y
el período de conmutación.

$t=1/f_s = 66,66 \ \mu s$

$$I_g = \frac{Q_g}{t} = \frac{97 \ nC}{66,66 \ \mu s} = 1,455 \ mA$$

$$R_{max} = \frac{V_{in}}{I_g} = \frac{12 \ V}{1,455 \ mA} = 8,25 \ k\Omega$$

Este valor fue probado en simulación pero generaba una disminución drástica en el tiempo de respuesta del 
transistor, por ello se probará en la práctica para determinar si este cálculo es adecuado o no.

## Diseño Prototipo 12 V

Circuito

Circuito de disparo

## Otro diseño - [Convertirdor 24 V](calculos_ganerales_24V_old.md)

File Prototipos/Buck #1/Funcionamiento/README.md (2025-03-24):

# Convertidor Buck

Circuito genérico del convertidor Buck

### Lista de Entradas-Salidas

<!-- 
| Señal | Tipo |
|----|-----|
| Tensión de alimentación | Entrada |
| Señal de control gate | Entrada |
| Tensión de salida | Salida |
| Tensión de retroalimentación | Salida |
-->

| Entrada | Salida |
|----|-----|
| Tensión de alimentación, $V_{cc}$ = 12 V | Tensión de salida, $V_{out}$ = 6 V|
| Señal de control gate, PWM -- 0 a 3,3 V | Tensión de retroalimentación, $V_\beta$ entre 0 y 3,3 V  |

El desarrollo siguiente fue obtenido de, [Electrical Technology](https://www.electricaltechnology.org/2020/09/buck-converter.html), 

## Resumen

Un convertidor Buck básico consiste en una conmutación controlada de un interruptor, un diodo, un filtro de salida, y un circuito de realimentación. El interruptor es el encargado de traspasar la potencia de entrada a la salida, dependiendo de la velocidad de conmutación o del tiempo que esté encendido, la tensión en la salida puede ser aumentar o disminuir, manteniéndose siempre por debajo de la tensión de entrada.

El voltaje medio de salida del convertidor puede ser controlado de 2 formas, PWM (pulse width modulation) o PFM (pulse frequency modulation). En el primero de los casos lo que se modifica es el tiempo de encendido, manteniéndose el periodo constante. A diferencia de PFM donde el periodo es el que se modifica (cambia la frecuencia de conmutación), pero el tiempo de encendido se mantiene constante, por ejemplo en un 50 % del duty. El método más elegido para los convertidores buck es el PWM.

Otro punto importante de los convertidores es el modo de operación, el mismo puede operar en dos modos de conducción, CCM (continuous conduction mode) y DCM (discontinuous conduction mode); en el primero la corriente en el inductor de salida permanece en un valor positivo, haciendo que nunca tenga corriente cero a través del mismo en el periodo de conmutación. En cambio para el caso de DCM, la corriente en el inductor se hace cero en algunos momentos del periodo de conmutación.

CCM-DCM

Si un convertidor fue diseñado para trabajar en modo CCM, también lo hará en modo DCM cuando al corriente por la carga disminuye.

Las imágenes siguientes fueron obtenidas de [Wikipedia](https://es.wikipedia.org/wiki/Convertidor_reductor#:~:text=El%20convertidor%20reductor%E2%80%8B%E2%80%8B,menor%20que%20a%20su%20entrada.).

CCM
DCM

## Funcionamiento

### Componentes principales del convertidor

* Interruptor, puede ser un transistor BJT como un MOSFET.
* Diodo de rectificación.
* Inductor.
* Capacitor de salida.
* Controlador PWM.

### Modo Encendido

Modo 1

En este momento el diodo queda polarizado de forma inversa, haciendo que toda la corriente de entrada se aplique en el inductor; el inductor se carga.

Modo 1 ondas

En la figura anterior se observa que, mientras el interruptor (en la mayoría de casos un transistor) conduce, la corriente a través del inductor aumenta llegando a su valor máximo; en el momento en que se apaga el interruptor la corriente comienza a disminuir.

### Modo Apagado

Modo 2

En este momento, el interruptor se encuentra abierto, y el inductor cambia su polaridad para oponerse a la descarga que está sufriendo el mismo, y el diodo queda polarizado en forma directa. 

### Medición de tensión

La medición de tensión es realizada mediante un divisor resistivo que reduce la tensión a un valor seguro para trabajarlo en el microcontrolador. Además se le anexa un filtro RC a la entrada del ADC para mejorar la medición del mismo. 

El objetivo de esta medición es poder realizar un control preciso de la tensión y corriente entregada a la carga, por ello se aplica un lazo cerrado donde la tensión de salida se la compara con una tensión de referencia (set-point), para así aplicar la corrección del ciclo de trabajo del PWM para lograr la conmutación correcta del transistor.

Si la carga demanda menos corriente, la tensión tiende a subir y viceversa, por ello la utilidad de un control para ajustar el D en función de la carga conectada al convertidor.

Hay diversas técnicas de control, dentro de las más utilizadas, PID.

## Red de Snubber

Red Snubber

Esta red es la encargada de reducir los picos de voltaje y de proteger al interruptor, frente a la rápida conmutación que realiza el mismo. Cuando el transistor conmuta en un periodo muy pequeño (alta frecuencia), se generan picos en $t_{on}$ y $t_{off}$ que son indeseados y empeoran el rendimiento del convertidor, por ello, se utiliza una red de Snubber, filtro RC que se encarga de filtrar esos altos picos de tensión debidos a la conmutación del interruptor.

Respuestas red Snubber

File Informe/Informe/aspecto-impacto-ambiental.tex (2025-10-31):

\section{Aspectos de impacto ambiental}
\justifying

Se denomina impacto ambiental a todo cambio que tiene lugar en el medio ambiente o en alguno de sus componentes, ya sea perjudicial o beneficioso, como resultado de una acción, conjunto de acciones o actividad. En este contexto, se considera que existe un impacto ambiental cuando existe una diferencia entre la situación del medio ambiente futuro producto de la realización de un proyecto, y la situación del medio ambiente futuro sin éste, \parencite{chaer2020impacto}.

En el presente proyecto, uno de los impactos ambientales negativos de mayor consideración es producto de las impresiones 3D, donde en lugar de utilizar un filamento biodegradable como lo es el PLA (ácido poliláctico), se utiliza el PETG (tereftalato de polietileno glicol), el cual es un filamento que presenta mayor resistencia mecánica, durabilidad y flexibilidad, además soporta mayores temperaturas antes de superar el umbral de deformación térmica. Si bien no es biodegradable como el PLA, el mismo es reciclable al \SI{100}{\percent}, \parencite{pla_petg}.

También se emplea en la elaboración del sistema un policarbonato transparente, utilizado como tapa de cada gabinete individual de los módulos. Este cumple la función de impedir que el usuario acceda con las manos a la PCB, y por otro lado, señalar los puntos de prueba disponibles dentro del módulo en uso. Es de destacar que el material fue cedido por UTN Facultad Regional San Francisco en forma de un retazo sobrante, lo que permite su reutilización y contribuye a reducir el impacto ambiental asociado al desecho de plásticos.

Además, se hizo uso de un transformador para reducir la tensión de línea doméstica, si bien la fabricación no está a cargo del grupo de trabajo, debe considerarse como un impacto ambiental total dentro del proyecto. El proceso de manufactura del transformador implica el consumo de materias primas, como el cobre y acero, además de la energía necesaria para las maquinarias utilizadas en el proceso. No obstante, al tratarse de un componente estándar y de larga vida útil, el impacto ambiental relacionado al mismo puede verse atenuado en el tiempo y reducido en relación al ciclo de vida del dispositivo completo.

El impacto ambiental respecto a la elaboración de las PCB se limita a la fabricación y transporte de los componentes desde la fábrica al proveedor, y desde el mismo a la ciudad de destino. Considerando el consumo del dispositivo, se tiene la fuente de alimentación de corriente continua y el transformador. La primera tiene un consumo máximo dependiendo de los módulos, siendo que los mismos se desarrollaron para \SI{12}{\volt} y \SI{3}{\ampere} máximos, dando así un consumo máximo de \SI{36}{\watt}. El transformador utilizado es de \SI{50}{\voltampere} con una potencia activa máxima de \SI{48}{\watt}. Para estimar el impacto energético asociado al uso del dispositivo, se considera la potencia máxima con un \SI{25}{\percent} adicional para abarcar el rendimiento de las etapas de potencia y cualquier pérdida no considerada.

\begin{equation} \label{eq:IA:potencia-total}
    P_{total} = (\SI{36}{\watt} + \SI{48}{\watt}) 1,25 = \SI{105}{\watt}
\end{equation}

Se trata de un consumo reducido, incluso menor que el de una computadora de escritorio en funcionamiento, lo que se traduce en una menor demanda energética y, en consecuencia, en un impacto ambiental reducido.

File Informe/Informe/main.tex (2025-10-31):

\documentclass[11pt, a4paper, fleqn]{article}

% Símbolos y lenguaje español %
\usepackage[utf8]{inputenc}
\usepackage[spanish]{babel}
\usepackage[babel]{microtype}
%\usepackage{times}       % Para usar Times New Roman
\usepackage{comment}     % Para comentarios en el código

% Márgenes %
\usepackage[left=2.5cm, right=1cm, top=3cm, bottom=2cm, bindingoffset=1cm]{geometry}

% Paquetes de matemática, símbolos y gráficos %
\usepackage{amsmath}
\usepackage{amssymb}
\usepackage{float}
\usepackage{mathtools} % Para splitfrac
%\usepackage{textcomp}
%\usepackage{gensymb}
\usepackage{xfrac}
%\usepackage{amsfonts}
\usepackage{siunitx}

% Declaración de unidades para siunitx %
\DeclareSIUnit{\voltampere}{VA}
\DeclareSIUnit{\voltpeak}{V_P}

% Tablas %
\usepackage{longtable}
\usepackage{tabularx}
\usepackage{float}
\newcolumntype{C}{>{\centering\arraybackslash}X}
\addto\captionsspanish{\renewcommand{\tablename}{Tabla}}

% Figuras %
\usepackage{graphicx}
\usepackage{subcaption}
\usepackage{tikz}
\usepackage{circuitikz}
\usepackage[justification = centering]{caption}
\graphicspath{{./figures/}}
\captionsetup{skip=0.25cm}
\usepackage{etoolbox}
\AfterEndEnvironment{figure}{\vspace{-0.5cm}} 
\BeforeBeginEnvironment{equation}{\vspace{-0.5cm}}
\BeforeBeginEnvironment{equation*}{\vspace{-0.5cm}}
\BeforeBeginEnvironment{align}{\vspace{-0.5cm}}

% Interlineado y sangría %
\usepackage[indent=0.5cm]{parskip}
\setlength{\mathindent}{0cm}
\usepackage{setspace}
\usepackage{indentfirst}
\onehalfspacing
\setlength{\parskip}{0.1cm}

% Encabezado y pie de página %
\usepackage{fancyhdr}
\pagestyle{fancy}
\setlength{\headheight}{70pt}
\addtolength{\topmargin}{-50pt}

\setlength{\headsep}{0cm}

\usepackage{wrapfig}
\usepackage[bottom]{footmisc}

% Paquetes para enumerar items %
\usepackage{enumitem}

% Paquetes de Bibliografía %
%\usepackage{xurl}
\usepackage[sorting=nyt,backend=biber,style=apa,urldate=long]{biblatex}
\usepackage{csquotes}

\bibliography{referencias}

% Hipervínculos %
\usepackage[hidelinks]{hyperref} % Agregar hidelinks para que no figure el recuadro

% Referencias cruzadas %
\usepackage[capitalise, nameinlink, spanish]{cleveref}
\crefname{table}{Tabla}{Tablas}

% Justificado %
\usepackage[]{ragged2e}

% Agregar PDFs %
\usepackage{pdfpages}

% Configuracion de secciones y subsecciones %
\usepackage{titlesec}
%\titleformat{\section}
%  [block]              % estilo de la sección
%  {\normalfont\bfseries\Large\centering} % formato del texto
%  {}                   % aquí va el número, lo dejamos vacío para no mostrar
%  {0pt}                % separación entre número (vacío) y título
%  {}                   % código antes del título

\titleformat
  {\paragraph} % Command
  [block]      % Shape
  {\normalfont\bfseries\normalsize} % Format
  {} % Label
  {0cm} % Separation
  {}
  []

\newcommand{\snsection}[1]{
  \section*{#1}
  \phantomsection
  \addcontentsline{toc}{section}{#1}
}
\newcommand{\snsubsection}[1]{
  \subsection*{#1}
  \phantomsection
  \addcontentsline{toc}{subsection}{#1}
}
\newcommand{\snsubsubsection}[1]{
  \subsubsection*{#1}
  \phantomsection
  \addcontentsline{toc}{subsubsection}{#1}
}

% Configuración para bibliografía
\setcounter{biburlnumpenalty}{100}
\setcounter{biburlucpenalty}{100}
\setcounter{biburllcpenalty}{100}
\appto{\bibsetup}{\emergencystretch=2em}

% Configuracion de la tabla de contenidos
%\usepackage{tocloft}

% ALEJO:  Hay que ver como hacer el índice porque si trabajas las secciones con \section*{title} por
% defecto las omite de la tabla de contenidos. Por eso despues de cada section*{}, \addcontentsline{toc}{section}{DEDICATORIA}
% el tema es que eso no me convence para nada, todavía no encontré un buen resultado como me gustaría.

% Rta Alejo para Alejo: Ya encontré la solución, el problema es que en lugar de usar \section*{} se usa \snsection{} y así
% se agrega automáticamente a la tabla de contenidos. Además, se puede usar \snsubsection{} y \snsubsubsection{} para subsecciones y subsubsecciones. Es la mejor solución que encontré para que los títulos de las secciones no tengan númeración y aparezcan en la tabla, sino la otra es directamente usar \section{} y que aparezcan los números y te evitas todo el inconveniente, pero no respetarías al 100% el formato APA

\begin{document}

    \pagenumbering{Roman}
    \input{encabezado_pdp}
    \input{portada}

    \input{dedicatoria}
    \newpage
    \input{resumen}
    \newpage

    % ÍNDICE ANTES DE INTRODUCCIÓN
    \renewcommand{\contentsname}{\Large ÍNDICE}
    \tableofcontents
    \newpage

    \pagenumbering{arabic}
    \input{introduccion}
    \newpage
    \input{metas}
    \newpage
    \input{descripcion}
    \newpage
    \input{objetivo}
    \newpage
    \input{justificacion}
    \newpage
    \input{alternativas-propuestas}
    \newpage
    \input{aspectos-mercado}
    \newpage
    \input{aspectos-financieros}
    \newpage
    \input{aspectos-institucionales}
    \newpage
    \input{aspecto-impacto-ambiental}
    \newpage
    \input{desarrollo}
    \newpage
    \input{conclusion}
    \newpage
    \input{apendice}
    \newpage

    %\renewcommand{\refname}{\Large REFERENCIAS}
    %\begin{minipage}{0.96\textwidth}
    %\phantomsection
    \addcontentsline{toc}{section}{Referencias}
    \printbibliography
    %\end{minipage}

    % DECLARACIÓN JURADA CON FIRMA NUESTRA, SUPONGO QUE SE HACE A MANO ESO
\end{document}

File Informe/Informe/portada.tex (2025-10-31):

\begin{titlepage}
    \centering

    \begin{center}
    \begin{minipage}{\textwidth}
        \centering
        \begin{tabular}[c]{@{}p{2cm}@{\hspace{0.5cm}}p{8.5cm}@{}}
        \raisebox{-0.75\height}{} &
        \begin{tabular}[t]{@{}l@{}}
            \Large\textbf{Universidad Tecnológica Nacional} \\[0.15cm]
            \large\textbf{Facultad Regional San Francisco} \\[0.15cm]
            \large Ingeniería Electrónica
        \end{tabular}
        \end{tabular}
    \end{minipage}
    \end{center}
    
    \vspace{2cm}

    \textbf{\huge Sistema Didáctico Modular para la Experimentación en Electrónica de Potencia}\\ [0.75cm]

     \\ [0.75cm]

    \textbf{\large{Autores:}}\\
    \textbf{Alesandria, Alejo Samuel}\\
    \textbf{Cignetti, Mateo Antonio}\\
    \textbf{Galliano, Ignacio}\\[0.25cm]
    
    \textbf{\large{Docente:}}\\
    \textbf{Ing. Musso, Daniel}\\[0.25cm]

    \textbf{\large{Tutores:}}\\
    \textbf{Dr. Ing. Pipino, Hugo}\\
    \textbf{Ing. Bossio, Jorge}\\[1cm]
    
    \textbf{\large{Fecha:}}\\
    \textbf{7 de noviembre de 2025}
    \vfill
\end{titlepage}

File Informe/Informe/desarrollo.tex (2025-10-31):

\input{desarrollo/gabinete.tex}
\input{desarrollo/diseno3D.tex}
\input{desarrollo/buck.tex}
\input{desarrollo/dimmer.tex}
\input{desarrollo/inversor.tex}
\input{desarrollo/pcb.tex}
\input{desarrollo/software.tex}
\input{desarrollo/escalabilidad.tex}
\input{desarrollo/resultados.tex}

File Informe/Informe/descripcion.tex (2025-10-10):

\section{Descripción}
\justifying

El proyecto consiste en el diseño y construcción de un sistema didáctico modular orientado a la enseñanza y aprendizaje de la electrónica de potencia. Está destinado a estudiantes y entusiastas que deseen experimentar con diferentes configuraciones de circuitos, tales como rectificadores, inversores, convertidores DC-DC, entre otros.

El sistema es comandado por un gabinete central que cuenta con una fuente de tensión de 12 V, un transformador de 220 V a 48 V, una PCB de control general con un microcontrolador ESP32-S3 y una interfaz compuesta por una pantalla y un encoder rotativo. El gabinete posee un cable con conector PCIe x4 hembra que permite la conexión de diferentes módulos funcionales. 

Se contempla el desarrollo de tres módulos funcionales. El diseño modular elegido facilita la expansión futura del sistema, permitiendo incorporar nuevos módulos personalizados conforme a las necesidades de los usuarios o los avances tecnológicos. Así, el proyecto se concibe como una plataforma abierta, adaptable y en constante evolución.

Los módulos desarrollados en este proyecto son los siguientes:
\begin{itemize}[noitemsep]
    \item Recortador de onda: regula la potencia entregada a la carga mediante el uso de un tiristor, recortando la onda de tensión. 
    \item Convertidor Buck: logra una tensión de salida menor a la tensión de entrada sin prescindir de eficiencia.
    \item Inversor de onda cuadrada: transfiere potencia desde una fuente de continua a una carga de alterna.
\end{itemize}

El sistema en su totalidad permite la observación de señales de entrada y salida con la ayuda de herramientas externas, así como el ajuste de parámetros en tiempo real, lo que posibilita un aprendizaje práctico e interactivo. A través de estas interacciones, se busca que los usuarios comprendan de forma tangible los principios fundamentales de la electrónica de potencia.

En el desarrollo del trabajo se implementó la metodología ágil Scrum, entendida como un marco de trabajo ligero que permite generar valor a través de soluciones adaptativas frente a problemas complejos, \parencite{SCRUM-GUIDE}. El trabajo se dividió en \textit{sprints}, permitiendo una planificación incremental y entregas periódicas. Además, se utilizó la función Proyectos de GitHub para gestionar una pizarra de tareas, organizando el flujo de trabajo en columnas: \textit{backlog}, \textit{ready}, \textit{in progress}, \textit{in review} y \textit{done}. Esto facilitó el seguimiento del avance, la asignación de responsabilidades y la colaboración entre los integrantes del equipo.

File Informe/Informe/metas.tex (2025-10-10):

\section{Meta}
\justifying

Este proyecto tiene como meta facilitar el aprendizaje práctico de electrónica de potencia mediante un sistema didáctico modular que permita la experimentación directa y el desarrollo de competencias a través de módulos especializados y material teórico complementario.

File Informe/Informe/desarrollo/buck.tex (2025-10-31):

\section{Módulo convertidor reductor o Buck}

Un convertidor es un circuito electrónico que transforma energía eléctrica de una forma a otra, ya sea cambiando niveles de tensión, corriente o frecuencia. En el caso del Buck, se trata de un tipo específico de convertidor DC-DC (\textit{Direct Current}, corriente continua en español) que disminuye la tensión de entrada a una menor en la salida, manteniendo una buena eficiencia gracias a su operación conmutada. Este convertidor funciona mediante el encendido y apagado rápido de un transistor, aprovechando elementos reactivos como inductores y capacitores para almacenar y transferir energía de manera controlada, evitando las pérdidas típicas de los reguladores lineales.

\subsection{Interacción del usuario: control y verificación experimental}

El usuario puede interactuar con el módulo mediante una interfaz intuitiva que permite seleccionar entre diferentes modos de control, como regulación automática de tensión mediante PID (control proporcional, integrador y derivativo) o ajuste manual del ciclo de trabajo PWM  (Pulse Frequency Modulation, modulación por frecuencia de pulso). Además, se puede modificar la frecuencia de conmutación y alternar entre una carga resistiva o inductiva usando el relé integrado. Se dispone de diversos \textit{test points} a través de la PCB con el fin de poder realizar pruebas en tiempo real utilizando herramientas de medición como osciloscopios, multímetros, entre otros.

Las principales señales que se observan en el módulo son: la tensión de salida (a través de la cual se puede observar la estabilidad de tensión frente a distintas condiciones de carga), la corriente en el inductor y la corriente de carga y descarga del capacitor. A su vez, se permite visualizar la señal de conmutación en el transistor, proporcionando así una experiencia completa para el aprendizaje y la caracterización del convertidor Buck.

El objetivo de esto es poner a disposición del usuario la mayor cantidad de pruebas posibles como, por ejemplo, analizar el efecto que produce una carga inductiva y resistiva sobre el PWM del microcontrolador, o el resultado en el \textit{ripple} debido al cambio de frecuencia de conmutación o al PWM. 

\subsection{Base teórica}

\begin{figure}[H]
    \centering
    \begin{tikzpicture}
        % Paths, nodes and wires:
        \draw (4.625, 15.125) to[american voltage source] (4.625, 13.125);
        \draw node[pigfete, solderdot, rotate=90] at (6.395, 15.625) {};
        \draw (7.875, 15.625) to[american inductor] (9.875, 15.625);
        \draw (7.625, 13.125) to[empty Schottky diode] (7.625, 15.125);
        \draw (10.125, 13.125) to[capacitor] (10.125, 15.125);
        \draw node[circ] at (7.625, 15.625) {};
        \draw node[circ] at (7.625, 15.625) {};
        \draw node[circ] at (7.625, 12.625) {};
        \draw node[circ] at (7.625, 12.625) {};
        \draw node[circ] at (10.125, 15.625) {};
        \draw node[circ] at (10.125, 15.625) {};
        \draw node[circ] at (10.125, 12.625) {};
        \draw node[circ] at (10.125, 12.625) {};
        \draw (7.625, 15.125) -| (7.625, 15.625);
        \draw (7.625, 13.125) -| (7.625, 12.625);
        \draw (10.125, 12.625) -| (10.125, 13.125);
        \draw (10.125, 15.125) -| (10.125, 15.625);
        \draw (4.625, 15.125) |- (5.125, 15.625) -- (5.625, 15.625);
        \draw (4.625, 13.125) -- (4.625, 12.625);
        \node[shape=rectangle, draw, line width=1pt, inner sep=0, minimum width=1.215cm, minimum height=0.965cm](Rect1) at (6.125, 13.625){} node[anchor=center] at (Rect1.center){$\mu C$};
        \draw node[circ] at (6.125, 14.125) {};
        \draw (6.125, 14.645) |- (6.125, 14.125);
        \node[shape=rectangle, draw, line width=1pt, inner sep=0, minimum width=1.215cm, minimum height=1.215cm](Rect2) at (14.375, 14){} node[anchor=center] at (Rect2.center){$Carga$};
        \draw node[circ] at (14.375, 14.625) {};
        \draw node[circ] at (14.375, 13.375) {};
        \draw (11.625, 15.625) -| (14.375, 14.625);
        \draw (11.625, 12.625) -| (14.375, 13.375);
        \draw (4.625, 12.625) -- (10.125, 12.625);
        \draw (7.165, 15.625) -- (7.875, 15.625);
        \draw (9.875, 15.625) -- (10.125, 15.625);
        \draw (11.625, 15.625) to[american resistor] (11.625, 14.125);
        \draw (11.625, 14.125) to[american resistor] (11.625, 12.625);
        \draw (11.625, 15.625) -- (10.125, 15.625);
        \draw (11.625, 12.625) |- (10.125, 12.625);
        \draw node[circ] at (11.625, 15.625) {};
        \draw node[circ] at (11.625, 12.625) {};
        \draw node[circ] at (11.625, 14.125) {};
        \node[shape=rectangle, draw, line width=1pt, inner sep=0, minimum width=1.215cm, minimum height=0.965cm](Rect3) at (12.875, 13.375){} node[anchor=center] at (Rect3.center){$Retro$};
        \draw (11.625, 14.125) -- (12.375, 14.125) -| (12.875, 13.875);
        \draw node[circ] at (12.875, 13.875) {};
    \end{tikzpicture}
    \caption{Circuito básico del convertidor Buck.}
    \label{fig:buck:circuito_generico}
\end{figure}

Un convertidor Buck consta de un diodo, un filtro de salida, un circuito de realimentación y un interruptor al cual se le controla su conmutación, \cref{fig:buck:circuito_generico}; siendo el objetivo lograr una tensión de salida menor a la tensión de entrada sin prescindir de eficiencia. 

El interruptor se encarga de traspasar la potencia, de la entrada a la salida, dependiendo de la velocidad de conmutación o del tiempo que se encuentre encendido, la tensión en la salida puede aumentar o disminuir, pero manteniéndose siempre por debajo de la tensión de entrada, o en casos puede alcanzar el valor de la entrada, \parencite{RASHID}.

En este tipo de topología de convertidores DC-DC se suele emplear un transistor MOSFET canal p como interruptor en lugar de un MOSFET canal n, debido a la facilidad de implementación que entrega el primero mencionado. Para lograr que el transistor esté en conducción (MOSFET-p), es necesario tener una caída de tensión \textit{gate}-surtidor ($V_{gs}$) que cumpla con los rangos de operación del transistor, por ello el valor mínimo de tensión necesario para la conducción debe ser $V_{g(min)} = V_{in} - V_{gs(th)}$\protect\footnotemark, \cref{fig:buck:comparativa-transistor}\footnotetext{$V_{g}$, tensión de \textit{gate}. $V_{in}$, tensión de entrada.}. En cambio, el MOSFET-n requiere un circuito de mayor complejidad para ser disparado. A diferencia del canal p, para que el transistor canal n entre en zona de conducción se requiere que la tensión de \textit{gate} sea como mínimo $V_{g(min)} = V_{load} + V_{gs(th)}$\protect\footnotemark, \cref{fig:buck:comparativa-transistor}, aumentando así la dificultad para obtener este valor. El método utilizado para lograr esto se lo llama \textit{bootstrapping} o circuito de \textit{bootstrap}.
\footnotetext{$V_{load}$, tensión de carga.}

\begin{figure}[H]
    \centering
    \resizebox{0.7\textwidth}{!}{
        \begin{tikzpicture}
            % Paths, nodes and wires:
            \node[nigfete, rotate=90] at (9.731, 6.23){};
            \node[pigfete, rotate=90] at (9.73, 3.75){};
            \node[shape=rectangle, minimum width=2.34cm, minimum height=0.965cm] at (11.063, 5){} node[anchor=north west, align=left, text width=1.952cm, inner sep=6pt] at (9.875, 5.5){\textcolor{rgb,255:red,0;green,0;blue,255}{\scriptsize Gate \\ $V_{gs(th)}=\SI{2}{\volt}$}};
            \node[shape=rectangle, minimum width=1.465cm, minimum height=0.965cm] at (8.75, 6.25){} node[anchor=north west, align=left, text width=1.077cm, inner sep=6pt] at (8, 6.75){\textcolor{rgb,255:red,0;green,150;blue,70}{\scriptsize Drenador $\SI{12}{\volt}$}};
            \node[shape=rectangle, minimum width=1.215cm, minimum height=0.715cm] at (10.75, 6.375){} node[anchor=north west, align=center, text width=1cm, inner sep=6pt] at (10.125, 6.75){\scriptsize Surtidor};
            \node[shape=rectangle, minimum width=2.379cm, minimum height=0.985cm] at (10.543, 2.51){} node[anchor=north west, align=left, text width=1.991cm, inner sep=6pt] at (9.336, 3.02){\textcolor{rgb,255:red,0;green,0;blue,255}{\scriptsize Gate \\ $V_{gs(th)}=-\SI{2}{\volt}$ }};
            \node[shape=rectangle, minimum width=1.379cm, minimum height=1.235cm] at (8.793, 3.635){} node[anchor=north west, align=left, text width=0.991cm, inner sep=6pt] at (8.085, 4.27){\textcolor{rgb,255:red,0;green,150;blue,70}{\scriptsize Surtidor \\ $\SI{12}{\volt}$}};
            \node[shape=rectangle, minimum width=1.215cm, minimum height=0.695cm] at (10.55, 3.908){} node[anchor=north west, align=left, text width=1.5cm, inner sep=6pt] at (9.925, 4.273){\scriptsize Drenador};
            \node[shape=rectangle, draw, line width=1pt, minimum width=1.215cm, minimum height=0.715cm] at (12.5, 5.625){} node[anchor=center, align=center, text width=0.827cm, inner sep=6pt] at (12.5, 5.625){\footnotesize Carga};
            \draw (10.5, 6.23) -| (12.5, 6);
            \node[circ] at (12.5, 6){};
            \node[circ] at (12.5, 6){};
            \node[shape=rectangle, draw, line width=1pt, minimum width=1.175cm, minimum height=0.755cm] at (12.46, 3.145){} node[anchor=center, align=center, text width=0.787cm, inner sep=6pt] at (12.46, 3.145){\footnotesize Carga};
            \draw (10.5, 3.75) -| (12.46, 3.54);
            \node[circ] at (12.46, 3.54){};
            \node[circ] at (12.46, 3.54){};
            \node[shape=rectangle, minimum width=2.527cm, minimum height=0.465cm] at (7.281, 5.5){} node[anchor=north east, align=right, text width=2.139cm, inner sep=6pt] at (8.562, 5.75){\scriptsize MOSFET-n};
            \node[shape=rectangle, minimum width=2.59cm, minimum height=0.465cm] at (7.312, 3){} node[anchor=north east, align=right, text width=2.202cm, inner sep=6pt] at (8.625, 3.25){\scriptsize MOSFET-p};
            \node[shape=rectangle, minimum width=2.465cm, minimum height=0.965cm] at (14.5, 5.25){} node[anchor=north west, align=left, text width=2.077cm, inner sep=6pt] at (13.25, 5.75){\textcolor{rgb,255:red,255;green,0;blue,100}{\scriptsize Para disparar \\ $V_{g(min)}\geq \SI{14}{\volt}$}};
            \node[shape=rectangle, minimum width=2.465cm, minimum height=0.965cm] at (14.46, 2.75){} node[anchor=north west, align=left, text width=2.077cm, inner sep=6pt] at (13.21, 3.25){\textcolor{rgb,255:red,255;green,0;blue,100}{\scriptsize Para disparar \\ $V_{g(min)}\geq \SI{10}{\volt}$}};
        \end{tikzpicture}
    }
    \caption{MOSFET-n vs MOSFET-p.}
    \label{fig:buck:comparativa-transistor}
\end{figure}

Existen diversas formas de controlar el voltaje medio de salida del convertidor, entre las dos formas más conocidas se encuentra el PWM (Pulse Width Modulation, modulación por ancho de pulso) y el PFM, \cref{fig:buck:pfm_pwm}. En el primero de los casos lo que se modifica es el tiempo de encendido, manteniéndose el período constante. A diferencia de PFM donde el período es el que se modifica (cambia la frecuencia de conmutación), pero el tiempo de encendido se mantiene constante, por ejemplo, en un \SI{50}{\percent} del duty, \parencite{rohm-PWM-PFM}. El método más elegido para los convertidores Buck es el PWM.

\begin{figure}[H]
    \centering
    
    \caption{Tipos de modulaciones más usados.\\
    \textit{Fuente: \parencite{control-PFM-PWM}}}
    \label{fig:buck:pfm_pwm}
\end{figure}

Otro punto importante de los convertidores es el modo de operación, el mismo puede operar en dos formas, CCM (Continuous Conduction Mode, modo de conducción continua) y DCM (Discontinuous Conduction Mode, modo de conducción discontinua); en el primer caso, la corriente a través del inductor de salida se mantiene siempre positiva, sin alcanzar el valor cero durante el período de conmutación. En cambio, en el modo DCM, la corriente en el inductor llega a ser nula en determinados instantes del período de conmutación, \cref{fig:buck:CCM_DCM}.

Cuando el convertidor es controlado de forma digital, estos modos de conducción suelen presentarse dependiendo de la carga utilizada en el convertidor, de modo que a una carga de mayor consumo el convertidor actúa en modo CCM y para el caso contrario en DCM.

\begin{figure}[H]
    \centering
    
    \caption{Modos de funcionamiento.\\
    \textit{Fuente: \parencite{electricaltech-buck}}} 
    \label{fig:buck:CCM_DCM}
\end{figure}

\subsubsection{Funcionamiento del convertidor}

\paragraph{Modo encendido}

\begin{figure}[H]
    \centering
    \resizebox{0.8\textwidth}{!}{
        \begin{tikzpicture}
            % Paths, nodes and wires:
            \draw[draw=red] node[vee, rotate=90] (N1) at (5.817, 7.405) {} node[anchor=south east] at ([xshift=-0.1cm, yshift=-0.16cm]N1.south east){\textcolor{rgb,255:red,255;green,0;blue,0}{\small$I_L$}};
            \draw (2, 7) to[american voltage source, l_={$Vdc$}, label distance=0.02cm] (2, 4);
            \draw (2, 7) to[cute closed switch, l_={\small$On$}, label distance=-0.02cm] (4, 7);
            \draw (4.333, 6.504) to[bare jumper, l={\small$Vdc$}, label distance=-0.47cm,/tikz/circuitikz/bipoles/length=2.10cm] (4.333, 4.504);
            \draw[draw=red] (4.694, 7) to[cute inductor, l_={\textcolor{rgb,255:red,255;green,0;blue,0}{\small$V_L=V_S-V_O$}}, label distance=0.01cm] (6.444, 7);
            \draw[draw={rgb,255:red,0;green,180;blue,0}] (6.889, 6.5) to[curved capacitor] (6.889, 4.5);
            \draw[draw={rgb,255:red,140;green,0;blue,255}] (8.512, 6.425) to[american resistor, l={\textcolor{rgb,255:red,140;green,0;blue,255}{\small$ V_O$}}, label distance=0.02cm] (8.512, 4.425);
            \draw (6.889, 7) -| (8.512, 6.425);
            \draw (8.512, 4.425) |- (8.444, 4) |- (2, 4);
            \draw (4.333, 4.5) -| (4.333, 4);
            \draw (4.333, 6.5) -| (4.333, 7);
            \draw (6.889, 6.5) -| (6.889, 7);
            \draw (6.889, 4.5) -| (6.889, 4);
            \draw node[circ] at (4.333, 7) {};
            \draw node[circ] at (6.889, 7) {};
            \draw node[circ] at (6.889, 4) {};
            \draw node[circ] at (4.333, 4) {};
            \draw node[tground, xscale=0.5, yscale=0.5] at (4.583, 5.004) {};
            \draw node[plain crossing, xscale=0.63, yscale=0.63] at (4.583, 6.004) {};
            \draw[draw={rgb,255:red,140;green,0;blue,255}] node[plain crossing, xscale=0.63, yscale=0.63] at (8.835, 6.028) {};
            \draw[draw={rgb,255:red,140;green,0;blue,255}] node[tground, xscale=0.5, yscale=0.5] at (8.828, 4.764) {};
            \draw node[ground] at (2, 4) {};
            \draw node[circ] at (2, 4) {};
            \draw[draw={rgb,255:red,255;green,0;blue,0}] (5.817, 7.405) -| (5.142, 7.408);
            \draw[draw={rgb,255:red,0;green,180;blue,0}] node[vee] (N2) at (7.416, 5.411) {} node[anchor=south west] at ([xshift=-0.07cm, yshift=-0.07cm]N2.north){\textcolor{rgb,255:red,0;green,180;blue,0}{\small$I_C$}};
            \draw[draw={rgb,255:red,0;green,180;blue,0}] (7.416, 5.411) -| (7.419, 6.087);
            \draw (4, 7) -- (4.333, 7);
            \draw (4.333, 7) -- (4.694, 7);
            \draw (6.444, 7) -- (6.889, 7);
            \draw[draw={rgb,255:red,140;green,0;blue,255}] node[vee] (N3) at (9.441, 5.324) {} node[anchor=south west] at ([xshift=-0.16cm, yshift=-0.16cm]N3.north east){\textcolor{rgb,255:red,140;green,0;blue,255}{\small$I_R$}};
            \draw[draw={rgb,255:red,140;green,0;blue,255}] (9.441, 5.324) -| (9.444, 6);
            \node[shape=rectangle, draw={rgb,255:red,0;green,85;blue,255}, line width=0.8pt, inner sep=0, minimum width=5.185cm, minimum height=1.886cm] at (5.507, 5.275){};
            \draw[draw={rgb,255:red,0;green,85;blue,255}] node[vee, rotate=-90] at (5.667, 4.333) {};
            \draw[draw={rgb,255:red,0;green,85;blue,255}] node[vee, rotate=-90] at (7.778, 4.333) {};
            \draw[draw={rgb,255:red,0;green,85;blue,255}] node[vee, rotate=-180] at (2.913, 5.192) {};
            \draw[draw={rgb,255:red,0;green,85;blue,255}] node[vee, rotate=90] at (5.479, 6.222) {};
        \end{tikzpicture}
    }
    \caption{Interruptor en conducción.}
    \label{fig:buck:modo_encendido}
\end{figure}
En un primer momento, cuando el interruptor se encuentra abierto, la corriente en el circuito es nula; luego de cerrado por primera vez, la corriente comienza a incrementarse, por lo que el inductor genera una tensión opuesta en respuesta a la corriente de la fuente. En este momento, el diodo se encuentra polarizado de forma inversa, de modo que toda la corriente de entrada se aplica en el inductor, almacenando energía en forma de campo magnético, \cref{fig:buck:modo_encendido}.

El voltaje de caída mencionado contrarresta el voltaje de la fuente, generando una reducción en el voltaje a través de la carga. Luego de algunos ciclos de conmutación, la tasa de cambio de la corriente disminuye, y el voltaje a través del inductor también lo hace, haciendo que la tensión en la carga aumente.
\begin{figure}[H]
    \centering
    
    \caption{Tensión y corriente en el inductor.\\
    \textit{Fuente: \parencite{electricaltech-buck}}}
    \label{fig:buck:formas_onda}
\end{figure}
En la \cref{fig:buck:formas_onda} se observa que, mientras el interruptor conduce, la corriente a través del inductor aumenta llegando a su valor máximo. En el momento en que se apaga el interruptor la corriente comienza a disminuir.

\paragraph{Modo apagado}

Cuando el dispositivo de conmutación pasa a su estado de no conducción, la fuente es removida del circuito, haciendo que la corriente disminuya. La disminución de la corriente produce una caída de tensión en el inductor, inversa a la que había cuando se encontraba en estado de encendido, esto hace que la bobina funcione como una fuente de corriente hacia la carga por medio del campo magnético almacenado. Esta corriente solo fluye mientras la fuente se mantiene desconectada del circuito, \cref{fig:buck:modo_apagado}.

\begin{figure}[H]
    \centering
    \resizebox{0.8\textwidth}{!}{
        \begin{tikzpicture}
            % Paths, nodes and wires:
            \draw[draw=red] node[vee, rotate=90] (N1) at (5.817, 7.405) {} node[anchor=south east] at ([xshift=-0.1cm, yshift=-0.16cm]N1.south east){\textcolor{rgb,255:red,255;green,0;blue,0}{\small$I_L$}};
            \draw (2, 7) to[american voltage source, l_={$Vdc$}, label distance=0.02cm] (2, 4);
            \draw[draw=red] (4.694, 7) to[cute inductor, l_={\textcolor{rgb,255:red,255;green,0;blue,0}{\small$V_L=-V_O$}}, label distance=0.01cm] (6.444, 7);
            \draw[draw={rgb,255:red,0;green,180;blue,0}] (6.889, 6.5) to[curved capacitor] (6.889, 4.5);
            \draw[draw={rgb,255:red,140;green,0;blue,255}] (8.512, 6.425) to[american resistor, l={\textcolor{rgb,255:red,140;green,0;blue,255}{\small$V_O$}}, label distance=0.02cm] (8.512, 4.425);
            \draw (6.889, 7) -| (8.512, 6.425);
            \draw (8.512, 4.425) |- (8.444, 4) |- (2, 4);
            \draw (4.333, 4.5) -| (4.333, 4);
            \draw (4.333, 6.5) -| (4.333, 7);
            \draw (6.889, 6.5) -| (6.889, 7);
            \draw (6.889, 4.5) -| (6.889, 4);
            \draw node[circ] at (4.333, 7) {};
            \draw node[circ] at (6.889, 7) {};
            \draw node[circ] at (6.889, 4) {};
            \draw node[circ] at (4.333, 4) {};
            \draw[draw={rgb,255:red,140;green,0;blue,255}] node[plain crossing, xscale=0.63, yscale=0.63] at (8.835, 6.028) {};
            \draw[draw={rgb,255:red,140;green,0;blue,255}] node[tground, xscale=0.5, yscale=0.5] at (8.828, 4.764) {};
            \draw node[ground] at (2, 4) {};
            \draw node[circ] at (2, 4) {};
            \draw[draw={rgb,255:red,255;green,0;blue,0}] (5.817, 7.405) -| (5.142, 7.408);
            \draw[draw={rgb,255:red,0;green,180;blue,0}] node[vee] (N2) at (7.416, 5.411) {} node[anchor=south west] at ([xshift=-0.07cm, yshift=-0.07cm]N2.north){\textcolor{rgb,255:red,0;green,180;blue,0}{\small$I_C$}};
            \draw[draw={rgb,255:red,0;green,180;blue,0}] (7.416, 5.411) -| (7.419, 6.087);
            \draw (4, 7) -- (4.333, 7);
            \draw (4.333, 7) -- (4.694, 7);
            \draw (6.444, 7) -- (6.889, 7);
            \draw[draw={rgb,255:red,140;green,0;blue,255}] node[vee] (N3) at (9.441, 5.324) {} node[anchor=south west] at ([xshift=-0.16cm, yshift=-0.16cm]N3.north east){\textcolor{rgb,255:red,140;green,0;blue,255}{\small$I_R$}};
            \draw[draw={rgb,255:red,140;green,0;blue,255}] (9.441, 5.324) -| (9.444, 6);
            \draw (2.594, 7) to[cute open switch, l_={\small$Off$}, label distance=0.02cm] (3.406, 7);
            \draw (3.406, 7) -- (4, 7);
            \draw (2.594, 7) |- (2, 7);
            \draw (4.333, 6.5) -- (4.333, 4.5);
            \node[shape=rectangle, draw={rgb,255:red,0;green,85;blue,255}, line width=0.8pt, inner sep=0, minimum width=3.538cm, minimum height=1.886cm] at (6.325, 5.277){};
            \draw[draw={rgb,255:red,0;green,85;blue,255}] node[vee, rotate=-90] at (5.667, 4.333) {};
            \draw[draw={rgb,255:red,0;green,85;blue,255}] node[vee, rotate=-90] at (7.778, 4.333) {};
            \draw[draw={rgb,255:red,0;green,85;blue,255}] node[vee, rotate=-180] at (4.556, 5.222) {};
            \draw[draw={rgb,255:red,0;green,85;blue,255}] node[vee, rotate=90] at (7.333, 6.222) {};
        \end{tikzpicture}
    }
    \caption{Interruptor en estado de no conducción.}
    \label{fig:buck:modo_apagado}
\end{figure}

El interruptor se encuentra abierto, y el inductor cambia su polaridad para oponerse a la descarga que está sufriendo el mismo, quedando el diodo polarizado en forma directa.

Una vez que el convertidor se encuentra en un modo normal de funcionamiento, la corriente por la carga queda determinada por la suma de la corriente aportada por la fuente de alimentación, y por la corriente producto del campo magnético almacenado en el inductor. En este caso, siempre se tiene una corriente mayor en la carga. Ese aumento de corriente, debido a la corriente de fuente y a la corriente del inductor, da lugar a que el voltaje se vea disminuido en la carga para preservar la potencia del convertidor.

\subsection{Cálculos para el diseño}

El módulo convertidor reductor se diseña para una tensión de entrada de \SI{12}{\volt} y una corriente de entrada de \SI{3}{\ampere}. Para facilitar la visualización de las distintas señales, tanto de corriente como de tensión necesarias para la interpretación del circuito, la tensión de salida se establece con un rango completo de \SIrange{0}{12}{\volt}, al igual que la corriente. Esto permite que aumenten las posibilidades de pruebas en el laboratorio, y genera una mayor versatilidad para observar el funcionamiento del módulo en cuestión.

Los cálculos de diseño se basan en un informe de aplicación de \textit{Texas Instruments} \parencite{ti-buck-report}.

\paragraph{Criterios de diseño}

El módulo se calcula para una corriente de \SI{2,4}{\ampere} la cual representa un \SI{80}{\percent} de la corriente entregada por la fuente, esto es con el objetivo de mantener un margen de seguridad evitando exigir los componentes.

\begin{itemize}[noitemsep]
    \item Potencia del convertidor \SI{36}{\watt}.
    \item $R = \frac{\SI{12}{\volt}}{\SI{2.4}{\ampere}} = \SI{5}{\ohm}$.
    \item Ripple
    \begin{itemize}[noitemsep]
        \item $\Delta V_{out} = \SI{2}{\percent} ~ V_{out} = 0.02 \cdot \SI{12}{\volt} = \SI{0.24}{\volt}$
        \item $\Delta I_L = \SI{30}{\percent} ~ I_{out} = 0.3 \cdot \SI{2.4}{\ampere} = \SI{0.72}{\ampere}$
    \end{itemize}
    \item Frecuencia de conmutación ($f_s$), \SI{19}{\kilo\hertz}.
    \item Rendimiento teórico considerado, $\eta = \SI{90}{\percent}$.
\end{itemize}

Se elige como transistor de conmutación de potencia el IRF9540, \parencite{IRF9540}, la selección del mismo se basa en la disponibilidad y en su amplio campo de aplicación, lo que permite que en caso de falla o rotura del módulo sea fácil de reemplazar.

\subsubsection{Ciclo de trabajo máximo}
\vspace{-0.25cm}
\begin{equation} \label{eq:buck:duty_cycle}
    D_{max} = \frac{V_{out}}{V_{in} \, \eta} = \frac{\SI{6}{\volt}}{\SI{12}{\volt} \, 0.9} = 0.55    
\end{equation}

Dentro del cálculo es considerado el rendimiento porque el convertidor también entrega energía. Este cálculo proporciona un valor más realista del ciclo de trabajo máximo en comparación con la ecuación que no incluye el factor de rendimiento.

\subsubsection{Capacitor de salida mínimo}
\vspace{-0.25cm}
\begin{equation} \label{eq:buck:capacitancia_salida}
    C_{out_{min}} = \frac{\Delta I_L}{8 \, f_s \, \Delta V_{out}} = \frac{\SI{0,72}{\ampere}}{8 \cdot \, \SI{19e3}{\hertz} \, \SI{0.24}{\volt}} = \SI{19.74}{\micro\farad}
\end{equation}

Cualquier capacidad mayor a la calculada puede ser utilizada sin afectar el correcto funcionamiento del convertidor. Este tipo de cálculos se pueden realizar para convertidores con compensación externa. Para el caso de los internamente compensados, como puede ser un circuito integrado Buck, es recomendable utilizar los valores establecidos en la hoja de datos. El capacitor elegido para el circuito es de \SI{42}{\micro\farad}.

\subsubsection{Inductor mínimo}
\vspace{-0.25cm}
\begin{equation} \label{eq:buck:inductancia_minima}
    L_{min} = \frac{(V_{in}-V_{out}) \, D_{max}}{f_s \, \Delta I_L} = \frac{(\SI{12}{\volt} - \SI{6}{\volt}) \, 0.55}{\SI{19e3}{\hertz} \, \SI{0.72}{\ampere}} = \SI{241.23}{\micro\henry}
\end{equation}

El valor calculado se considera como mínimo, ya que emplear una inductancia mayor reduce el \textit{ripple} de corriente e incrementa la corriente de salida. Sin embargo, también implica un aumento en el tamaño físico del inductor. Por el contrario, disminuir la inductancia incrementa el \textit{ripple} y reduce la corriente de salida, aunque permite utilizar un inductor de menor tamaño. Por lo tanto, es necesario encontrar un equilibrio adecuado entre el tamaño del inductor y el nivel de \textit{ripple} permitido en la salida. Por ello, el inductor elegido para el circuito es de \SI{330}{\micro\henry}.

\subsubsection{Corriente media en diodo}
\vspace{-0.25cm}
\begin{equation} \label{eq:buck:corriente_diodo_rectificacion}
    I_D = I_{out} \, (1-D) = \SI{2.4}{\ampere} \, (1-0.55) = \SI{1.08}{\ampere}
\end{equation}

Este valor determina la corriente media aplicada en el diodo de rectificación, es recomendable utilizar un Schottky ya que su rápida recuperación lo hace adecuado a las altas frecuencias de trabajo del convertidor. Además, la tensión soportada por el diodo debe ser al menos un \SI{30}{\percent} más que la tensión de salida del convertidor.

El diodo elegido para cumplir estas características es el SR560, \parencite{SR560}.

\subsubsection{Red Snubber}

El cálculo de la red Snubber se basa en una nota de aplicación de Toshiba \parencite{toshiba_2018_power}, tomando como referencia algunos de sus criterios, además de criterios propios.

Se supone un valor de inductancia parásita típico de 50 nH y que la capacitancia parásita es $C_P = C_{OSS}$, siendo $C_{OSS}$ la capacitancia de salida del transistor.

$f_{ring}$, representa la frecuencia de las oscilaciones existentes en la conmutación del transistor, no se tiene este valor, pero se calcula en función de un valor estimado de inductancia parásita, con el fin de probar el circuito con red de snubber y sin la misma.

\paragraph{Red de Snubber para transistor IRF9540}

$C_{OSS} = 400 \ pF \approx C_{snub}(min)$

\begin{equation} \label{eq:buck:frecuencia-oscilacion-mos-snubber}
    f_{ring} = \frac{1}{2 \pi * \sqrt{L_P * C_P}} = \SI{35.6}{\mega\hertz}
\end{equation}

\begin{equation} \label{eq:buck:resistencia-mos-snubber}
    R_{snub} = \frac{1}{2\pi f_{ring} C_{snub}} = \SI{11.2}{\ohm}
\end{equation}

\paragraph{Red de Snubber para transistor 2N2222}

$C_{obo} = 8 \ pF \approx C_{snub}(min)$. $C_{obo}$, capacitancia de salida de transistores BJT.

\begin{equation} \label{eq:buck:frecuencia-oscilacion-bjt-snubber}
    f_{ring} = \frac{1}{2 \pi * \sqrt{L_P * C_P}} = \SI{251.65}{\mega\hertz}
\end{equation}

\begin{equation} \label{eq:buck:resistencia-bjt-snubber}
    R_{snub} = \frac{1}{2\pi f_{ring} C_{snub}} = \SI{79}{\ohm}
\end{equation}

Los cálculos que se presentan a continuación, siguen la técnica descrita en un artículo técnico de \textit{Texas Instruments}, \parencite{ti_2016_snubber}. Este método consiste en probar el circuito en dos condiciones, la primera es sin ninguna red de Snubber para poder determinar la frecuencia de oscilación real; la segunda condición es conectando un capacitor en paralelo al transistor y medir la frecuencia nuevamente. El objetivo de esta prueba es que al conectar el capacitor, la frecuencia medida sea de al menos un \SI{50}{\percent} menor a la frecuencia real de oscilación del circuito. 

La tensión medida es entre colector y emisor de un transistor BJT, o entre drenador y surtidor de un transistor MOSFET. Estas oscilaciones que se presentan en las \cref{fig:buck:freq-oscilacion-bjt,fig:buck:freq-oscilacion-mosfet}, son las que aparecen en el momento en el que los transistores cambian su estado, de encendido a apagado o viceversa. Esta frecuencia es la denominada anteriormente como frecuencia de \textit{ring}, la cual no es deseada, teniendo que disminuir al máximo su efecto.

\begin{figure}[H]
    \centering
    \begin{subfigure}[b]{0.49\textwidth} % Aumenté un poco el ancho para que sea más robusto
        \centering
        
        \caption{Sin capacitor.}
        \label{fig:buck:freq-oscilacion-mos-sin-cap}
    \end{subfigure}
    \hfill 
    \begin{subfigure}[b]{0.49\textwidth}
        \centering
        
        \caption{Con capacitor de \SI{400}{\pico\farad}.}
        \label{fig:buck:freq-oscilacion-mos-con-cap}
    \end{subfigure}
    \caption{Resultados en transistor IRF9540 en circuito real}
    \label{fig:buck:freq-oscilacion-mosfet}
\end{figure}

\begin{figure}[H]
    \centering
    \begin{subfigure}[b]{0.49\textwidth} % Aumenté un poco el ancho para que sea más robusto
        \centering
        
        \caption{Sin capacitor.}
        \label{fig:buck:freq-oscilacion-bjt-sin-cap}
    \end{subfigure}
    \hfill 
    \begin{subfigure}[b]{0.49\textwidth}
        \centering
        
        \caption{Con capacitor de \SI{2}{\pico\farad}\protect \footnotemark.}
        \label{fig:buck:freq-oscilacion-bjt-con-cap}
    \end{subfigure}
    \caption{Resultados en transistor 2N2222 en circuito real}
    \label{fig:buck:freq-oscilacion-bjt}
\end{figure}
\footnotetext{Se utiliza un capacitor de \SI{2}{\pico\farad} en lugar del utilizado para el cálculo en la \cref{eq:buck:frecuencia-oscilacion-bjt-snubber}, ya que el corrimiento necesario de frecuencia fue más coherente con el mismo.}

En las \cref{fig:buck:freq-oscilacion-mosfet,fig:buck:freq-oscilacion-bjt} se puede observar el corrimiento de frecuencia necesario para los siguientes cálculos.

\paragraph{Nuevos valores para red de Snubber de transistor IRF9540}

Datos para la obtención de nuevos valores de red de Snubber:
    \begin{itemize}[noitemsep]
        \item Frecuencia de oscilación sin capacitor, $f_0 = \SI{19.23}{\mega\hertz}$, \cref{fig:buck:freq-oscilacion-mos-sin-cap}.
        \item Frecuencia de oscilación con capacitor, $f_1 = \SI{11.9}{\mega\hertz}$, \cref{fig:buck:freq-oscilacion-mos-con-cap}.
        \item Capacitor paralelo, $C_1 = \SI{400}{\pico\farad}$.
    \end{itemize} 

\begin{equation*}
    m = \frac{f_0}{f_1} = 1.62
\end{equation*}

Se calcula la capacitancia e inductancia parásita.

\begin{equation*}
    C_0 = \frac{C_1}{m^2 - 1} = \SI{246.24}{\pico\farad}
\end{equation*}

\begin{equation*}
    L = \frac{m^2 - 1}{\left(2\pi \, f_0\right)^2 \, C_1} = \SI{278.17}{\nano\henry}
\end{equation*}

Se determinan los nuevos valores de red de Snubber en función del corrimiento de frecuencia.

\begin{equation} \label{eq:buck:cap-snub-mosfet}
    C_{snub} = 3 \, C_0 = \SI{738.72}{\pico\farad}
\end{equation}

\begin{equation} \label{eq:buck:res-snub-mosfet}
    R_{snub} = \sqrt{\frac{L}{C_0}} = \SI{33.61}{\ohm}
\end{equation}

Se utiliza un valor de \SI{1}{\nano\farad} para el capacitor y de \SI{33}{\ohm} para la resistencia de la red.

\paragraph{Nuevos valores para red de Snubber de transistor 2N2222}

Datos para la obtención de nuevos valores de red de Snubber:

\begin{itemize}[noitemsep]
    \item Frecuencia de oscilación sin capacitor, $f_0 = \SI{19.23}{\mega\hertz}$, \cref{fig:buck:freq-oscilacion-bjt-sin-cap}.
    \item Frecuencia de oscilación con capacitor, $f_1 = \SI{12.05}{\mega\hertz}$, \cref{fig:buck:freq-oscilacion-bjt-con-cap}.
    \item Capacitor paralelo, $C_1 = \SI{2}{\pico\farad}$.
\end{itemize} 

\begin{equation*}
    m = \frac{f_0}{f_1} = 1.6
\end{equation*}

Se calcula la capacitancia e inductancia parásita.

\begin{equation*}
    C_0 = \frac{C_1}{m^2 - 1} = \SI{1.28}{\pico\farad}
\end{equation*}

\begin{equation*}
    L = \frac{m^2 - 1}{\left(2\pi \, f_0\right)^2 \, C_1} = \SI{53.43}{\nano\henry}
\end{equation*}

Se determinan los nuevos valores de red de Snubber en función del corrimiento de frecuencia.

\begin{equation} \label{eq:buck:cap-snub-bjt}
    C_{snub} = 3 \, C_0 = \SI{3.84}{\pico\farad}
\end{equation}

\begin{equation} \label{eq:buck:res-snub-bjt}
    R_{snub} = \sqrt{\frac{L}{C_0}} = \SI{6460.82}{\ohm}
\end{equation}

Se utiliza un valor de \SI{5}{\pico\farad} para el capacitor y de \SI{6.8}{\kilo\ohm} para la resistencia de la red.
%\end{comment}

En las \cref{fig:buck:freq-oscilacion-mosfet-nueva,fig:buck:freq-oscilacion-bjt-nueva} se encuentran los resultados con los nuevos valores de red de Snubber, donde se puede determinar una amplia disminución de la frecuencia de oscilación no deseada en la conmutación de los transistores.

\begin{figure}[H]
    \centering
    \begin{subfigure}[b]{0.49\textwidth} % Aumenté un poco el ancho para que sea más robusto
        \centering
        
        \caption{Únicamente con capacitor en paralelo, \cref{fig:buck:freq-oscilacion-mos-con-cap}.}
        \label{fig:buck:freq-oscilacion-mos-con-cap-nueva}
    \end{subfigure}
    \hfill 
    \begin{subfigure}[b]{0.49\textwidth}
        \centering
        
        \caption{Con nuevos valores de red de \\ Snubber.}
        \label{fig:buck:tension-snub-nueva-mosfet}
    \end{subfigure}
    \caption{Resultados en transistor IRF9540 en circuito real}
    \label{fig:buck:freq-oscilacion-mosfet-nueva}
\end{figure}

\begin{figure}[H]
    \centering
    \begin{subfigure}[b]{0.49\textwidth} % Aumenté un poco el ancho para que sea más robusto
        \centering
        
        \caption{Únicamente con capacitor en paralelo, \cref{fig:buck:freq-oscilacion-bjt-con-cap}.}
        \label{fig:buck:freq-oscilacion-bjt-con-cap-nueva}
    \end{subfigure}
    \hfill 
    \begin{subfigure}[b]{0.49\textwidth}
        \centering
        
        \caption{Con nuevos valores de red de \\ Snubber.}
        \label{fig:buck:tension-snub-nueva-bjt}
    \end{subfigure}
    \caption{Resultados en transistor 2N2222 en circuito real}
    \label{fig:buck:freq-oscilacion-bjt-nueva}
\end{figure}

\subsubsection{Realimentación microcontrolador}

Para poder realizar un control digital es necesario tener una variable manipulada y una controlada. La primera, para el caso del convertidor Buck, es el PWM que se aplica al terminal \textit{gate} del transistor MOSFET-p; la segunda se corresponde a la tensión de salida realimentada al microcontrolador. 

Para lograr realimentar la tensión de salida se utiliza un divisor de tensión, encargado de adecuar la tensión de salida con rango \SIrange{0}{12}{\volt}, a tensiones manejables por el microcontrolador, rango \SIrange{0}{3.3}{V}. En la \cref{eq:buck:resistencia_divisor_tension} se presenta el cálculo de las resistencias del divisor de tensión, donde $R_1$ es la resistencia que se conecta entre la salida y el punto medio del divisor, y $R_2$ es la resistencia que se conecta entre el punto medio y tierra; se presenta gráficamente en la \cref{fig:buck:divisor_tensión}.

\begin{align} \label{eq:buck:resistencia_divisor_tension}
    V_{out} =& \frac{V_{in} \, R_2}{R_1+R_2} \\
    \SI{3.3}{\volt} =& \frac{\SI{12}{\volt} \, \SI{4.7}{\kilo\ohm}}{R_1+\SI{4.7}{\kilo\ohm}} \nonumber \\
    R_1 =& \SI{12.39}{\kilo\ohm} \nonumber
\end{align}

\begin{figure}[htb]
    \centering
    \resizebox{0.3\linewidth}{!}{
        \begin{circuitikz}
            % Paths, nodes and wires:
            \draw (2, 6) to[american resistor, l={$R_1$}, label distance=0.02cm] (2, 3);
            \draw (2, 3) to[american resistor, l={$R_2$}, label distance=0.02cm] (2, -0);
            \draw node[sground] (gnd) at (2, -0) {} node[anchor=north] at (gnd.south){\small$GND$};
            \node[shape=rectangle, draw, line width=1pt, inner sep=0, minimum width=3.465cm, minimum height=0.965cm] at (5.25, 3){} node [anchor=center, align=center, text width=3.077cm, inner sep=5.5pt] at (5.25, 3){Microcontrolador};
            \draw (2, 3) -- (3.5, 3);
            \draw node[vcc] (N1) at (2, 6) {} node[anchor=south] at (N1.north){\SI{12}{\volt}};
        \end{circuitikz}
    }
    \caption{Divisor de tensión genérico.}
    \label{fig:buck:divisor_tensión}
\end{figure}

\subsubsection{Filtro RC para ADC}

\paragraph{Criterios de diseño - filtro pasa-bajos}

\begin{itemize}[noitemsep]
    \item $f_c = \SI{100}{\hertz}$
    \item $C = \SI{10}{\micro\farad}$
    \item $f_c = \frac{1}{2\pi \, R \, C}$
\end{itemize}

\begin{equation} \label{eq:buck:resistencia_filtro_adc}
    R = \frac{1}{2\pi \, f_c \, C} = \SI{159.15}{\ohm} \approx \SI{150}{\ohm}
\end{equation}

En la \cref{fig:buck:filtro_adc} se presenta el filtro pasa-bajos utilizado en la entrada del ADC del microcontrolador, este filtro también es conocido como RC.

\begin{figure}[H]
    \centering
    \resizebox{0.45\linewidth}{!}{
        \begin{circuitikz}
            % Paths, nodes and wires:
            \draw (2, 7) to[american resistor, l={$R$}, label distance=0.02cm] (5, 7);
            \draw (5, 7) to[capacitor, l={$C$}, label distance=0.02cm] (5, 4);
            \draw (2, 4) -- (6.75, 4);
            \draw (5, 7) -- (6.75, 7);
            \draw node[circ] at (5, 7) {};
            \draw node[circ] at (5, 7) {};
            \draw node[circ] at (5, 4) {};
            \draw node[circ] at (5, 4) {};
            \draw node[ocirc] at (2, 7) {};
            \draw node[ocirc] at (2, 7) {};
            \draw node[ocirc] at (2, 4) {};
            \draw node[ocirc] at (2, 4) {};
            \draw node[ocirc] at (6.75, 4) {};
            \draw node[ocirc] at (6.75, 4) {};
            \draw node[ocirc] at (6.75, 7) {};
            \draw node[ocirc] at (6.75, 7) {};
            \node[shape=rectangle, inner sep=0, minimum width=2.5cm, minimum height=1.25cm] at (2, 5.5){} node [anchor=center, align=center, text width=2.147cm, inner sep=5pt] at (2, 5.5){Entrada};
            \node[shape=rectangle, inner sep=0, minimum width=2.5cm, minimum height=1.25cm] at (6.75, 5.5){} node [anchor=center, align=center, text width=2.147cm, inner sep=5pt] at (6.75, 5.5){Salida};
        \end{circuitikz}
    }
    \caption{Filtro pasa-bajos genérico.}
    \label{fig:buck:filtro_adc}
\end{figure}

Tanto el filtro como el divisor de tensión anteriormente mencionados, \cref{fig:buck:divisor_tensión,fig:buck:filtro_adc}; y calculados, \cref{eq:buck:resistencia_divisor_tension,eq:buck:resistencia_filtro_adc}, son importantes para poder realizar correctamente un control digital.

El objetivo de esta medición es poder realizar un control preciso de la tensión entregada a la carga, por ello se aplica un lazo cerrado donde la tensión de salida se la compara con una tensión de referencia (\textit{setpoint}), para así aplicar la corrección del ciclo de trabajo del PWM y lograr la conmutación correcta del transistor. Si la carga demanda menos corriente, la tensión tiende a subir y viceversa, por ello la utilidad de un control para ajustar el ciclo de trabajo en función de la carga conectada al convertidor. Hay diversas técnicas de control, dentro de las más utilizadas, PID.

\subsubsection{Transistor BJT como driver de MOSFET}

Como el microcontrolador elegido es el ESP32-S3, el mismo presenta en la hoja de datos que la corriente acumulada de todos los pines es de \SI{1.5}{\ampere}, por ende, si el microcontrolador posee 45 pines físicos, cada uno cuenta de \SI{33.33}{\milli\ampere} de corriente. El transistor elegido para este uso es el 2N2222, posee una corriente de colector máxima de \SI{600}{\milli\ampere} y un $\beta$ de 100 para una corriente de colector de \SI{150}{\milli\ampere}.

\begin{equation} \label{eq:buck:resistencia_limitadora_corriente}
    R_{b(min)} = \frac{V}{I_{b}} = \frac{\SI{3.3}{\volt}}{\frac{\SI{150}{\milli\ohm}}{100}} = \SI{2.2}{\kilo\ohm}
\end{equation}

Se elige una resistencia de \SI{2.2}{\kilo\ohm}, \cref{fig:buck:bjt_driver_mosfet}. La principal función de utilizar esta resistencia es limitar la corriente que se demanda al microcontrolador, pero a su vez es necesaria para que tanto el microcontrolador como el transistor no se dañen debido a corrientes indeseadas o parásitas mayores a la corriente deseada para el correcto funcionamiento. Una consideración por tener es que, cuanto mayor es el valor de resistencia, el tiempo de respuesta del transistor disminuye.

\begin{figure}[H]
    \centering
    
    \caption{Transistor 2N2222 como driver de MOSFET-p.}
    \label{fig:buck:bjt_driver_mosfet}
\end{figure}

\subsubsection{Mediciones de corriente} \label{sec:buck:medicion_corriente}

\paragraph{Medición de corriente en inductor - Unidireccional}

Para facilitar la medición de corriente y poder visualizar el comportamiento de la misma en operación normal del convertidor, se utiliza un amplificador de corriente INA199B2, el cual es un amplificador operacional utilizado en su configuración diferencial, \cref{fig:buck:ina199_unidireccional} \parencite{ina199_datasheet}.

\begin{figure}[H]
    \centering
    
    \caption{Medición de corriente unidireccional con INA199B2.}
    \label{fig:buck:ina199_unidireccional}
\end{figure}

\paragraph{Información útil para cálculos}

\begin{itemize}[noitemsep]
    \item Ganancia = \SI[per-mode=symbol]{100}{\volt\per\volt}.
    \item $V_{CC} = \SI{5}{\volt}$.
    \item $V_{out}= \SIrange{0.05}{4.8}{\volt}$.
\end{itemize}

Información obtenida de la hoja de datos del amplificador INA199B2, \parencite{ina199_datasheet}.

\paragraph{Criterio de diseño}

\begin{itemize}[noitemsep]
    \item $V_{R_{shunt}} = \SIrange{20}{50}{\milli\volt}$.
    \item $R_{shunt} = \SIrange{6.8}{15}{\milli\ohm}$.
    \item $P_{R_{shunt}} = \SIrange{61.2}{135}{\milli\watt}$. 
\end{itemize}

Estos valores fueron calculados para una corriente de \SI{3}{\ampere}, que es la corriente máxima determinada para el diseño del convertidor.

En una primera instancia se calcula el valor máximo de tensión en la resistencia \textit{shunt}, $V_{R_{shunt}}$, teniendo en cuenta la tensión de salida máxima del integrado, $V_{out} = \SI{4.8}{\volt}$; y la ganancia del amplificador, $Ganancia = 100$; \cref{eq:buck:salida_amplificador_unidireccional}.

\begin{align} \label{eq:buck:salida_amplificador_unidireccional}
    V_{out} =& Ganancia \, V_{R_{shunt}} \\
    \SI{4.8}{\volt} =& 100 \, V_{R_{shunt}} \nonumber \\ 
    V_{R_{shunt}} =& \frac{\SI{4.8}{\volt}}{100} = \SI{48}{\milli\volt}\nonumber 
\end{align}

Luego se determina el valor de la resistencia \textit{shunt}, $R_{shunt}$, a partir de la tensión máxima en la resistencia \textit{shunt} y la corriente máxima del convertidor, \cref{eq:buck:resistencia_shunt_unidireccional}.

\begin{equation} \label{eq:buck:resistencia_shunt_unidireccional}
    R_{shunt} = \frac{V_{R_{shunt}}}{I_{out(max)}} = \frac{\SI{48e-3}{\volt}}{\SI{3}{\ampere}} = \SI{0,016}{\ohm}
\end{equation}

Se elige una resistencia \textit{shunt} de $\SI{10}{\milli\ohm}$ por la disipación de potencia. Además, entrega un buen rango de tensión a la salida del amplificador, $V_{out} = \SIrange{0.05}{3}{\volt}$.

\paragraph{Medición de corriente en capacitor - Bidireccional}

Como la corriente en el capacitor es bidireccional, se debe realizar un arreglo de resistencias al amplificador de corriente para poder medir este tipo de corriente, \cref{fig:buck:ina199_bidireccional}. 

Es común en esta configuración de amplificador diferencial la necesidad de utilizar una tensión de referencia del \SI{50}{\percent} de la tensión de alimentación del integrado, con el fin de lograr que la corriente en la resistencia \textit{shunt} pueda ser medida en ambos sentidos. Cuando $V_{shunt} < V_{ref}$ la corriente circula en un sentido, y cuando $V_{shunt} > V_{ref}$ la corriente circula en sentido contrario al anterior. 

Para lograr la tensión de referencia se usa un divisor de tensión para obtener el voltaje requerido, $\SI{2,5}{\volt}$; a su vez se aplica un operacional como seguidor de tensión por recomendación propia del fabricante.

\begin{figure}[H]
    \centering
    
    \caption{Medición de corriente bidireccional con INA199B2.}
    \label{fig:buck:ina199_bidireccional}
\end{figure}

\paragraph{Criterio de diseño}

\begin{itemize}[noitemsep]
    \item $V_{ref} =$ $\frac{\SI{5}{\volt} \, \SI{10}{\kilo\ohm}}{\SI{10}{\kilo\ohm} + \SI{10}{\kilo\ohm}} = \SI{2.5}{\volt}$.
\end{itemize}

\begin{align} \label{eq:buck:salida_amplificador_bidireccional}
    V_{out} =& V_{ref} + Ganancia \, V_{R_{shunt}} \\
    \SI{4.8}{\volt} =& \SI{2,5}{\volt} + 100 \, V_{R_{shunt}} \nonumber \\
    V_{R_{shunt}} =& \frac{\SI{4.8}{\volt} - \SI{2.5}{\volt}}{100} = \SI{0.023}{\volt} \nonumber
\end{align}

\begin{equation} \label{eq:buck:resistencia_shunt_bidireccional}
    R_{shunt} = \frac{V_{R_{shunt}}}{I_{load}} = \frac{\SI{23}{\milli\volt}}{\SI{3}{\ampere}} = \SI{7,67}{\milli\ohm}
\end{equation}

El procedimiento presentado en las \cref{eq:buck:salida_amplificador_bidireccional,eq:buck:resistencia_shunt_bidireccional} es similar al realizado para la medición de corriente unidireccional, con la única diferencia del voltaje de referencia, $V_{ref}$, fijado por el divisor de tensión.

Se opta por utilizar una resistencia \textit{shunt} de \SI{5}{\milli\ohm}, ya que si se eligiese una resistencia mayor, la tensión entregada por el amplificador estaría muy próxima al valor máximo manejable por el mismo; además es un valor comercial común y estandarizado, fácil de conseguir.

\subsubsection{Selección de carga con Relé}

Para experimentar el comportamiento del convertidor Buck frente a diferentes cargas, se utiliza un relé controlado por un microcontrolador permitiendo elegir entre dos cargas: una resistiva y otra inductiva, con el fin de notar las diferencias que puede causar un simple cambio de carga en la operación normal del convertidor.

Para conmutar entre los dos estados del relé, normal abierto o normal cerrado, se utiliza un transistor BJT como \textit{driver}, \cref{fig:buck:driver_rele}.

\begin{figure}[H]
    \centering
    
    \caption{Circuito \textit{driver} para relé.}
    \label{fig:buck:driver_rele}
\end{figure}

\subsubsection{Cálculo de disipador para MOSFET de conmutación}

Una vez seleccionado el transistor MOSFET-p es necesario determinar la disipación de potencia que experimenta en la operación normal del convertidor. Para ello, se divide la potencia total en resistiva y de conmutación. Como lo indica el nombre, la primera se debe a la resistencia drenador-surtidor de transistor; y la segunda es debido a la conmutación del mismo en la operación del convertidor Buck, \parencite{analog-devices-power-dissipation}.

\begin{equation} \label{eq:buck:potencia_total}
    P_{total} = P_{resistive} + P_{switching} 
\end{equation}

Para determinar si es necesario el uso de un disipador en el transistor, el primer paso es asumir una temperatura de juntura máxima, respetando el rango determinado por la hoja de datos. Para el caso del IRF9540 se asume una temperatura de juntura de $T_{J(hot)} = \SI{120}{\degreeCelsius}$ \protect \footnotemark.
\footnotetext{Para este cálculo, se mantienen los valores de temperatura en grados Celsius, ya que solo intervienen en diferencias matemáticas.}

Una vez determinado este valor se procede a calcular el valor de $R_{DS(on)}$ con el valor elegido de temperatura de juntura.

\begin{align} \label{eq:buck:resistencia_ds_hot}
    R_{DS(on)hot} =& R_{DS(on)spec} \, \left[ 1 + 0.005 \, (T_{J(hot)}-T_{spec}) \right] \\
    =& \SI{0.117}{\ohm} \, \left[ 1 + 0.005 \, (\SI{120}{\degreeCelsius} - \SI{25}{\degreeCelsius}) \right] \nonumber \\
    =& \SI{0.172}{\ohm} \nonumber
\end{align}

Luego, se calcula la potencia disipada debido a la resistencia anteriormente calculada.

\begin{align} \label{eq:buck:potencia_resistiva}
    P_{resistive} =& \left[ I_{load}^2 \, R_{DS(on)hot} \right] \, \frac{V_{out}}{V_{in}} \\
    =& \left[ (\SI{3}{\ampere})^2 \, \SI{0.172}{\ohm}\right] \, 1 \nonumber \\
    =& \SI{1,55}{\watt} \nonumber
\end{align}

A su vez, se determina cuánta potencia se disipa debido a la conmutación del transistor.

\begin{align} \label{eq:buck:potencia_conmutación}
    P_{switching} =& \frac{C_{rss} \, V_{in}^2 \, f_{sw} \, I_{load}}{I_{gate}} \\
    =& \frac{\SI{240}{\pico\farad} \, (\SI{12}{\volt})^2 \, \SI{19}{\kilo\hertz} \, \SI{3}{\ampere}}{\SI{100}{\milli\ampere}} \nonumber \\
    =& \SI{0.02}{\watt} \nonumber
\end{align}

Partiendo de la \cref{eq:buck:potencia_total} se obtiene la potencia que debe disipar el transistor MOSFET-p. Los valores están calculados para una potencia de salida de \SI{36}{W}.

\begin{equation*}
    P_{total} = \SI{1.55}{\watt} + \SI{0.02}{\watt} = \SI{1.57}{\watt}
\end{equation*}

\paragraph{Resistencia térmica}

Partiendo de la potencia total, es requisito determinar cuánto es el aumento de la temperatura de juntura debido a la potencia disipada.

\begin{align} \label{eq:buck:temperatura_juntura_rise}
    T_{J(rise)} =& P_{total} \, \Theta_{JA} \\
    =& \SI{1.57}{\watt} \, \SI[per-mode=symbol]{62}{\celsius\per\watt} \nonumber \\
    =& \SI{97.22}{\celsius} \nonumber
\end{align}

Luego se debe determinar el valor de la temperatura ambiente teórica que debe existir para lograr la temperatura de juntura anteriormente calculada.

\begin{align} \label{eq:buck:temperatura_ambiente}
    T_{ambiente} =& T_{J(hot)} - T_{J(rise)} \\
    =& \SI{120}{\celsius} - \SI{97.22}{\celsius} \nonumber \\
    =& \SI{22.78}{\celsius} \nonumber
\end{align}

Si la temperatura ambiente real excede la temperatura ambiente calculada, $T_{ambiente} = \SI{22.78}{\degreeCelsius}$, es necesario emplear un disipador térmico. Debido a que esta temperatura es ligeramente menor a \SI{25}{\degreeCelsius}, se emplea un pequeño disipador de $17\times11\times5 \, \unit{\milli\meter}$.

\subsubsection{Eficiencia del convertidor}

La eficiencia es un término útil para determinar cuánto de la potencia que se entrega al convertidor es traspasada a la salida del mismo, se expresa en un porcentaje. Alternativamente, se puede expresar la eficiencia en término de las pérdidas, \cref{eq:buck:rendimiento}; \parencite{ti-eficiencia}.

\begin{equation} \label{eq:buck:rendimiento}
    \eta = \frac{P_O}{P_O + P_D}  
\end{equation}

Las pérdidas por disipación incluyen tanto las de conmutación y conducción del transistor, como así también las que respectan al núcleo magnético del inductor. Las pérdidas parásitas en capacitores, o pistas del circuito no se las considera para el cálculo ya que son valores despreciables, en comparación a las otras pérdidas mencionadas.

\begin{equation} \label{eq:buck:potencia_inductor}
    P_L = I_O^2 \, R_{DCR} = (\SI{3}{\ampere})^2 \, \SI{150}{\milli\ohm} = \SI{1.35}{\watt}
\end{equation}

Una vez calculada la disipación debido al núcleo magnético del inductor, \cref{eq:buck:potencia_inductor} y la disipación total producto del transistor de conmutación, \cref{eq:buck:potencia_total}; se puede calcular la potencia disipativa o de pérdidas teórica que tiene el circuito, \cref{eq:buck:potencia_disipativa}.

\begin{equation} \label{eq:buck:potencia_disipativa}
    P_D = P_L + P_{total} = \SI{1.35}{\watt} + \SI{1.55}{\watt} = \SI{2.9}{\watt}
\end{equation}

El rendimiento teórico del convertidor está dado por, \cref{eq:buck:rendimiento_teorico_calculado}.

\begin{align} \label{eq:buck:rendimiento_teorico_calculado}
    \eta &= \frac{P_O}{P_O + P_D} \\
    &= \frac{\SI{36}{\watt}}{\SI{36}{\watt} + \SI{2.9}{\watt}} \nonumber \\
    &= 0.925 \approx \SI{92,5}{\percent}
\end{align}

\subsection{Simulación}

Para corroborar el correcto funcionamiento del circuito previo a su elaboración física, se realiza la simulación del mismo utilizando el software gratuito LTspice, \parencite{LTSPICE}.

\begin{figure}[H]
    \centering
    \begin{subfigure}[b]{0.49\textwidth} % Aumenté un poco el ancho para que sea más robusto
        \centering
        
        \caption{Tensión en drenador.}
        \label{fig:buck:simulacion-1}
    \end{subfigure}
    \begin{subfigure}[b]{0.49\textwidth}
        \centering
        
        \caption{Tensión de salida en simulación.}
        \label{fig:buck:simulacion-2}
    \end{subfigure}
  
    \begin{subfigure}[b]{\columnwidth}
        \centering
        
        \caption{Circuito utilizado para simular\protect \footnotemark.}
        \label{fig:buck:circuito_simulacion}
    \end{subfigure}
    \caption{Resultados de la simulación con un ciclo de trabajo del \SI{50}{\percent}.}
    \label{fig:buck:resultados-simulacion}
\end{figure}
\footnotetext{Se utilizó el diodo RBR5LAM60A por disponibilidad del modelo para simulación. Las características se corresponden con las de SR560.}

Como se observa en la \cref{fig:buck:resultados-simulacion} el circuito funciona según lo esperado, donde al aplicar un ciclo de trabajo del \SI{50}{\percent} aproximadamente, la tensión de salida es de \SI{6}{\volt}. Cabe aclarar que las \cref{fig:buck:simulacion-1,fig:buck:simulacion-2} están tomadas en régimen permanente, sin considerar los posibles efectos transitorios del circuito.

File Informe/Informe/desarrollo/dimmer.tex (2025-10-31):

\section{Módulo recortador de onda}

Uno de los métodos más simples para controlar la potencia entregada a una carga de corriente alterna es mediante el uso de un recortador. Este método se basa en la utilización de un tiristor para recortar la onda de tensión aplicada a la carga, permitiendo así regular la potencia entregada. Al recortar la onda, se reduce la tensión RMS aplicada a la carga, lo que a su vez produce una reducción de potencia entregada.

Este método tiene varias desventajas, como una baja eficiencia y alta distorsión armónica. Sin embargo, su simplicidad y bajo costo es la razón por la cual se sigue utilizando en aplicaciones específicas donde se requiere un control de potencia simple y económico.

Se elige este módulo para el proyecto ya que es un buen primer paso en la electrónica de potencia, donde se puede realizar un enfoque centralizado en el funcionamiento y control de un semiconductor como el TRIAC (Triode for Alternating Current, Triodo para Corriente Alterna en español).

\subsection{Interacción del usuario: control y verificación experimental}

El módulo recortador de onda está diseñado para que el usuario pueda seleccionar entre dos modos de control: analógico y digital. En el modo de control analógico, el usuario utiliza un potenciómetro dentro del gabinete para modificar una resistencia, lo que cambia el tiempo de carga de un capacitor y el tiempo de disparo del TRIAC, variando la potencia entregada a la carga (dos lámparas de \SI{24}{\volt} en serie). En el modo de control digital, el usuario puede directamente elegir el tiempo de disparo del TRIAC, en base al cruce por cero de la tensión de corriente alterna de entrada. Mediante distintos puntos de prueba, el usuario puede con un osciloscopio visualizar diferentes ondas, como la tensión aplicada a la carga, tensión en TRIAC, carga y descarga de capacitor, entre otras. De esta manera, el usuario aprende sobre el funcionamiento del circuito y verificar experimentalmente los conceptos teóricos.

\subsection{Base teórica}

\subsubsection{Tiristores y el TRIAC}

Los tiristores pueden adoptar diversas formas, pero comparten ciertas características. Todos son interruptores de estado sólido que actúan como circuitos abiertos capaces de soportar la tensión nominal hasta su activación. Al activarse, los tiristores se convierten en circuitos de corriente de baja impedancia y permanecen en esa condición hasta que la corriente se detiene o cae por debajo de un valor mínimo denominado nivel de retención. Una vez activado un tiristor, la corriente de activación puede eliminarse sin apagar el dispositivo, \parencite{ON-ThyristorHandbook}

El TRIAC es un tiristor bidireccional ampliamente utilizado en la electrónica de potencia, en especial en aplicaciones menores a 40 A. Puede ser pensado como dos SCR (Silicon Controlled Rectifier, Rectificador controlado de silicio en español) en antiparalelo con su terminal de compuerta unidos. Además, puede ser disparado por una señal de corriente alterna o una de corriente continua positiva o negativa.

\subsubsection{Características del TRIAC}
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

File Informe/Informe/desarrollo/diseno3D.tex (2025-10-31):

\section{Diseño de gabinetes de módulos}

Para la construcción de los gabinetes de cada módulo y del gabinete general del prototipo, se opta por la impresión 3D, ya que esta tecnología permite fabricarlos a medida con las especificaciones requeridas, además de ofrecer costos accesibles y una rápida producción. Los diseños se realizan en FreeCAD \parencite{FreeCAD}, seleccionado por ser un software libre, fácil de usar y altamente versátil.
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

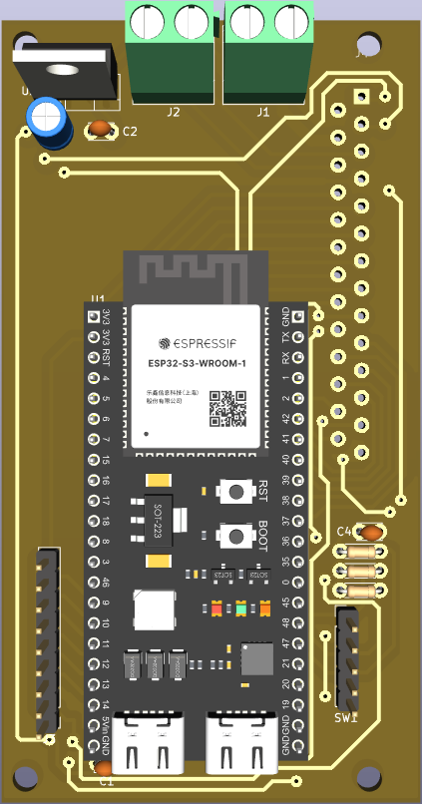
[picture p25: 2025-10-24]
Informe/Informe/figures/pcb/pcbgeneral_front.png

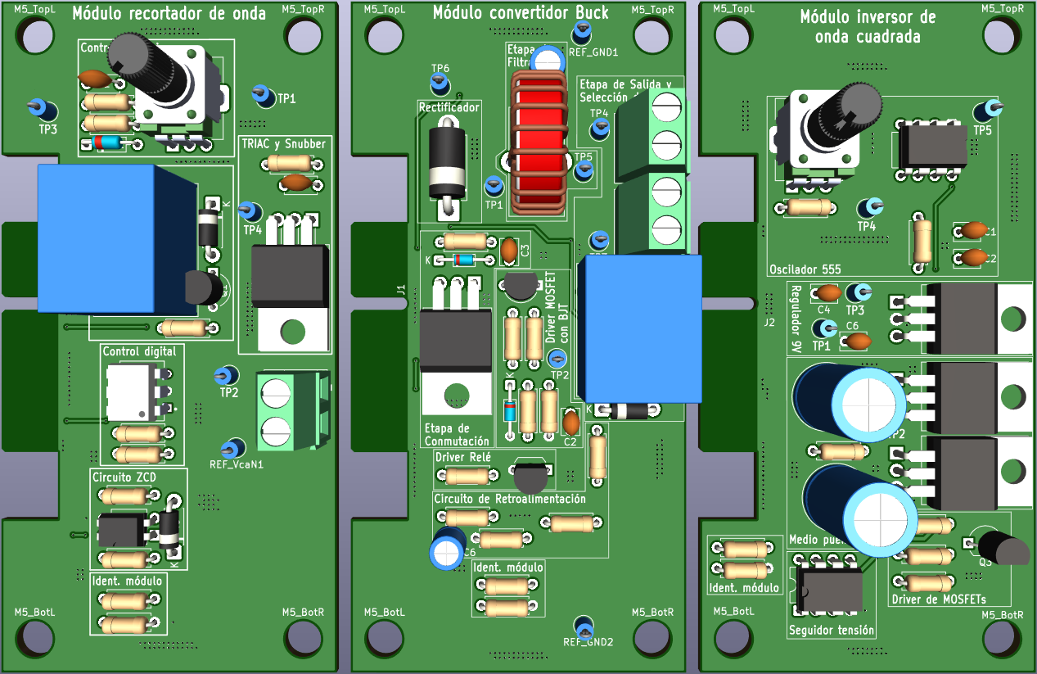
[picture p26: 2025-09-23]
Informe/Informe/figures/pcb/modulos_front.png

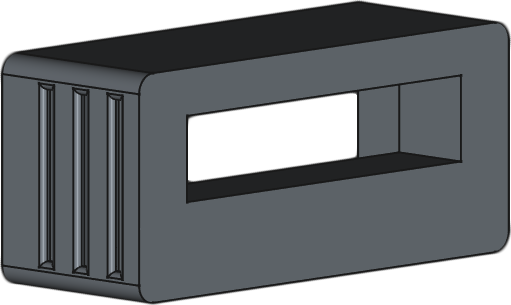
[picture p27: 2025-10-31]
Informe/Informe/figures/3d/Carcasa_conector.png

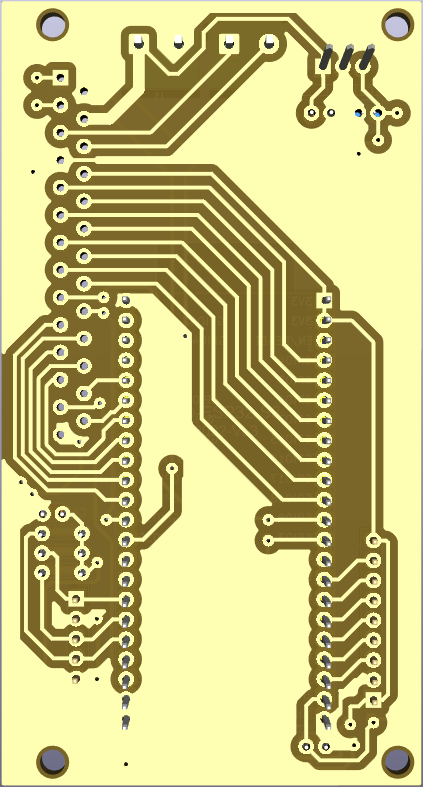
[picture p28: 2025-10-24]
Informe/Informe/figures/pcb/pcbgeneral_back.png

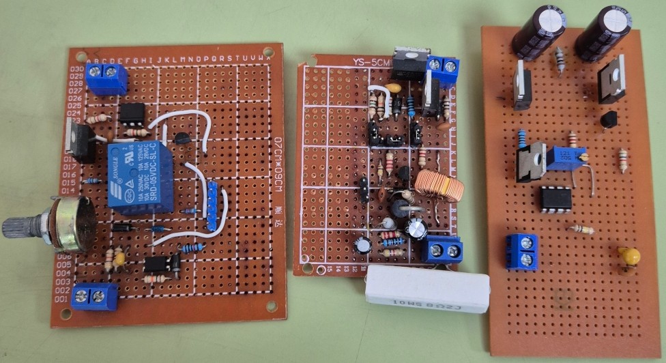
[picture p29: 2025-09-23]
Informe/Informe/figures/pcb/foto_placas_perforadas.jpg

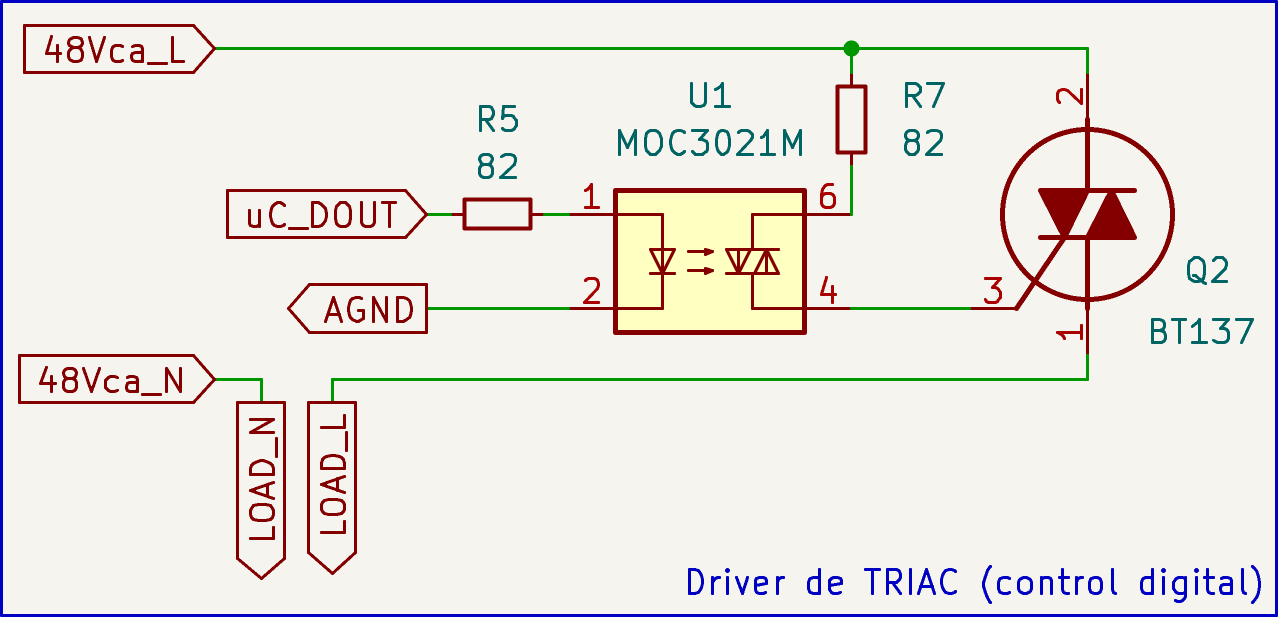
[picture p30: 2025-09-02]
Informe/Informe/figures/dimmer/driver_triac_cd.png

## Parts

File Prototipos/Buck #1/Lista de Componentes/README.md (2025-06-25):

# Lista de componentes - Prototipo de Convertidor Buck 12 V

| Elemento | Valor / Modelo | Cantidad |
|:---:|:---:|:---:|
| Capacitor Cerámico | 2 pF (red de Snubber) | 1 |
| Capacitor Cerámico | 400 pF (red de Snubber) | 1 |
| Capacitor Cerámico | 1 uF | 1 |
| Capacitor electrolítico | 10 uF | 1 |
| Capacitor electrolítico | 42 uF | 1 |
| Diodo Schottky | Cualquiera (1N5819) | 3 |
| Diodo Schottky | Cualquiera (SR560) | 1 |
| Diodo común | Cualquiera | 1 |
| Inductor | 370 $\mu$ H (preferentemente 5 A) | 1 |
| Resistencia THT 1/4 W | 12 $\Omega$ (red de Snubber) | 1 |
| Resistencia THT 1/4 W | 120 $\Omega$ | 1 |
| Resistencia THT 1/4 W | 150 $\Omega$ | 1 |
| Resistencia THT 1/4 W | 180 $\Omega$ (red de Snubber) | 1 |
| Resistencia THT 1/4 W | 2,2 k $\Omega$ | 2 |
| Resistencia THT 1/4 W | 4,7 k $\Omega$ | 1 |
| Resistencia THT 1/4 W | 10 k $\Omega$ | 2 |
| Resistencia THT 1/4 W | 12 k $\Omega$ | 1 |
| Resistencia THT 1/4 W | 15 k $\Omega$ | 1 |
| Resistencia THT 1/4 W | 100 k $\Omega$ | 1 |
| Terminal 01x02 | Cualquiera | 2 |
| Transistor BJT NPN | BC548 | 1 |
| Transistor BJT NPN | 2N2222 | 1 |
| Transistor MOSFET canal P | IRF9540 | 1 |
| Relé 5V CC | SRD-05VDC-SL-C | 1 |

Para la utilización de otros transistores revisar [hoja de cálculos](../Cálculos/README.md)

La red de Snubber del diodo de rectificación no se encuentra calculada, a determinar los valores.
Los capacitores y los inductores de las demás redes de Snubber habría que tener varios para probar cual va mejor.

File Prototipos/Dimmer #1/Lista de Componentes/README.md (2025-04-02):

# Lista de componentes - Prototipo Dimmer #1

| Elemento | Valor / Modelo | Cantidad |
|:---|:---:|:---:|
| Capacitor cerámico | 10 nF | 1 |
| Capacitor cerámico | 100 nF | 1 |
| DIAC | DB3 | 1 |
| Diodo genérico | Cualquiera | 2 |
| Optoacoplador | EL817 | 1 |
| OptoTRIAC | MOC3021M | 1 |
| Potenciómetro lineal |  100 $k\Omega$ | 1 |
| Relé 5V CC | SRD-05VDC-SL-C | 1 |
| Resistencia THT 1/4 W &plusmn;5% | 51 $\Omega$  | 1 |
| Resistencia THT 1/4 W &plusmn;5% | 82 $\Omega$  | 2 |
| Resistencia THT 1/4 W &plusmn;5% |  1 $k\Omega$ | 1 |
| Resistencia THT 1/4 W &plusmn;5% |  1,8 $k\Omega$ | 1 |
| Resistencia THT 1/4 W &plusmn;5% |  10 $k\Omega$  | 1 |
| Resistencia THT 1/4 W &plusmn;5% |  12 $k\Omega$  | 1 |
| Resistencia THT 1/4 W &plusmn;5% |  150 $k\Omega$ | 1 |
| Terminal 2x1 |  Cualquiera | 2 |
| Tira de pines macho  6x1 |  Cualquiera | 1 |
| Transistor BJT NPN | BC548B | 1 |
| TRIAC | BT137 | 1 |

En caso de reemplazar algún componente por otro similar, ver la [hoja de cálculos](../Cálculos/README.md)

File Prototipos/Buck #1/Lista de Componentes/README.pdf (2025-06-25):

## Lista de componentes - Prototipo de Convertidor Buck 12 V

Elemento | Valor / Modelo | Cantidad
Capacitor Cerámico | 2 pF (red de Snubber) | 1
Capacitor Cerámico | 400 pF (red de Snubber) | 1
Capacitor Cerámico | 1 uF | 1
Capacitor electrolítico | 10 uF | 1
Capacitor electrolítico | 42 uF | 1
Diodo Schottky | Cualquiera (1N5819) | 3
Diodo Schottky | Cualquiera (SR560) | 1
Diodo común | Cualquiera | 1
Inductor | 370 µ H (preferentemente 5 A) | 1
Resistencia THT 1/4 W | 12 Ω (red de Snubber) | 1
Resistencia THT 1/4 W | 120 Ω | 1
Resistencia THT 1/4 W | 150 Ω | 1
Resistencia THT 1/4 W | 180 Ω (red de Snubber) | 1
Resistencia THT 1/4 W | 2,2 k Ω | 2
Resistencia THT 1/4 W | 4,7 k Ω | 1
Resistencia THT 1/4 W | 10 k Ω | 2
Resistencia THT 1/4 W | 12 k Ω | 1
Resistencia THT 1/4 W | 15 k Ω | 1
Resistencia THT 1/4 W | 100 k Ω | 1
Terminal 01x02 | Cualquiera | 2
Transistor BJT NPN | BC548 | 1
Transistor BJT NPN | 2N2222 | 1
Transistor MOSFET canal P | IRF9540 | 1
Relé 5V CC | SRD-05VDC-SL-C | 1

Para la utilización de otros transistores revisar hoja de cálculos

La red de Snubber del diodo de rectificación no se encuentra calculada, a determinar los valores. Los capacitores y los inductores de las demás redes de Snubber habría que tener varios para probar cual va mejor.

1

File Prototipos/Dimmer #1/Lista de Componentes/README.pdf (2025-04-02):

## Lista de componentes - Prototipo Dimmer #1

Elemento | Valor / Modelo | Cantidad
Capacitor cerámico | 10 nF | 1
Capacitor cerámico | 100 nF | 1
DIAC | DB3 | 1
Diodo genérico | Cualquiera | 2
Optoacoplador | EL817 | 1
OptoTRIAC | MOC3021M | 1
Potenciómetro lineal | 100 kΩ | 1
Relé 5V CC | SRD-05VDC-SL-C | 1
Resistencia THT 1/4 W ±5% | 51 Ω | 1
Resistencia THT 1/4 W ±5% | 82 Ω | 2
Resistencia THT 1/4 W ±5% | 1 kΩ | 1
Resistencia THT 1/4 W ±5% | 1,8 kΩ | 1
Resistencia THT 1/4 W ±5% | 10 kΩ | 1
Resistencia THT 1/4 W ±5% | 12 kΩ | 1
Resistencia THT 1/4 W ±5% | 150 kΩ | 1
Terminal 2x1 | Cualquiera | 2
Tira de pines macho 6x1 | Cualquiera | 1
Transistor BJT NPN | BC548B | 1
TRIAC | BT137 | 1

En caso de reemplazar algún componente por otro similar, ver la hoja de cálculos

1

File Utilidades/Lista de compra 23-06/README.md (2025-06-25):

# Lista de compra de componentes efectuada el 23 de junio de 2025

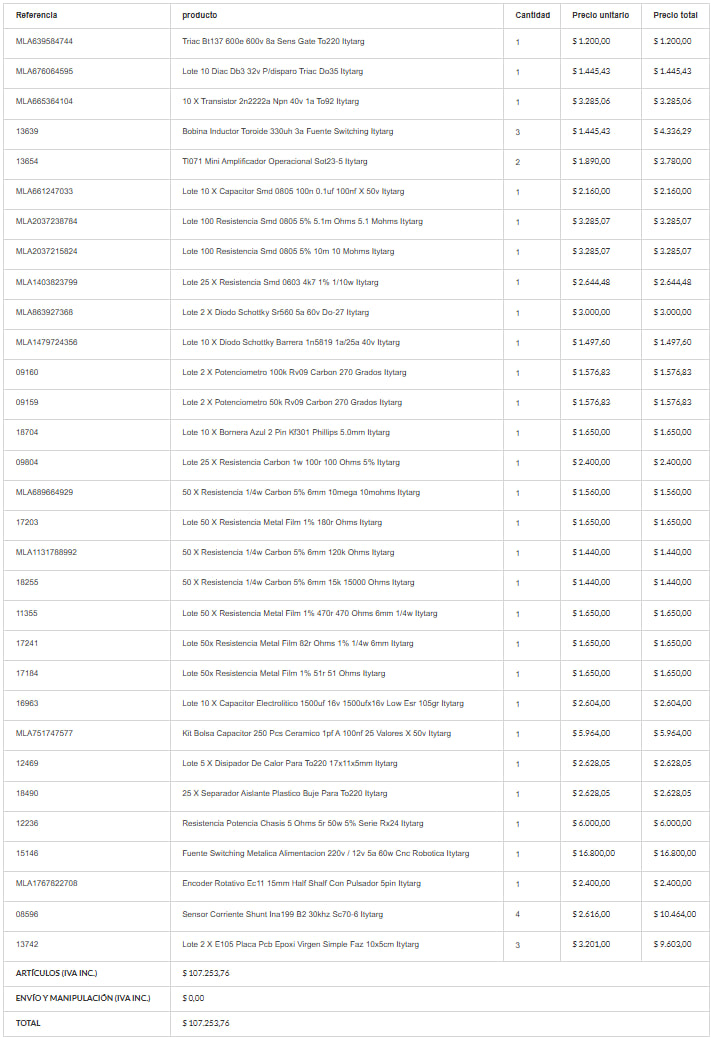
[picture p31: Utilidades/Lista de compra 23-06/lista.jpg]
lista-compra


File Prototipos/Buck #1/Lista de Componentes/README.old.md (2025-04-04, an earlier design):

# Lista de componentes - Prototipo de Convertidor Buck 12 V

| Elemento | Valor / Modelo | Cantidad  |
|:---:|:---:|:---:|
| Capacitor Cerámico | 2 pF | 1 |
| Capacitor Cerámico | 65 pF | 1 |
| Capacitor Cerámico | 400 pF | 1 |
| Capacitor Cerámico | 1 uF | 1 |
| Capacitor Cerámico | 10 uF | 1 |
| Capacitor Cerámico | 42 uF | 1 |
| Diodo Schottky | Cualquiera | 3 |
| Diodo Schottky | Cualquiera 1 A | 1 |
| Inductor | 370 $\mu$ H | 1 |
| Resistencia THT 1/4 W | 12 $\Omega$ | 1 |
| Resistencia THT 1/4 W | 27 $\Omega$ | 1 |
| Resistencia THT 1/4 W | 120 $\Omega$ | 1 |
| Resistencia THT 1/4 W | 150 $\Omega$ | 2 |
| Resistencia THT 1/4 W | 180 $\Omega$ | 1 |
| Resistencia THT 1/4 W | 1 k $\Omega$ | 2 |
| Resistencia THT 1/4 W | 2,2 k $\Omega$ | 1 |
| Resistencia THT 1/4 W | 4,7 k $\Omega$ | 1 |
| Resistencia THT 1/4 W | 10 k $\Omega$ | 1 |
| Resistencia THT 1/4 W | 33 k $\Omega$ | 1 |
| Terminal 01x02 | Cualquiera | 2 |
| Tira de pines macho 01x03 | Cualquiera | 4 |
| Transistor BJT NPN | BC548 | 1 |
| Transistor MOSFET canal N | IRLML6344 | 1 |
| Transistor MOSFET canal P | IRF9540 | 1 |

Para la utilización de otros transistores revisar [hoja de cálculos](../Cálculos/README.md)

El diodo no se encuentra calculado, valores a determinar.

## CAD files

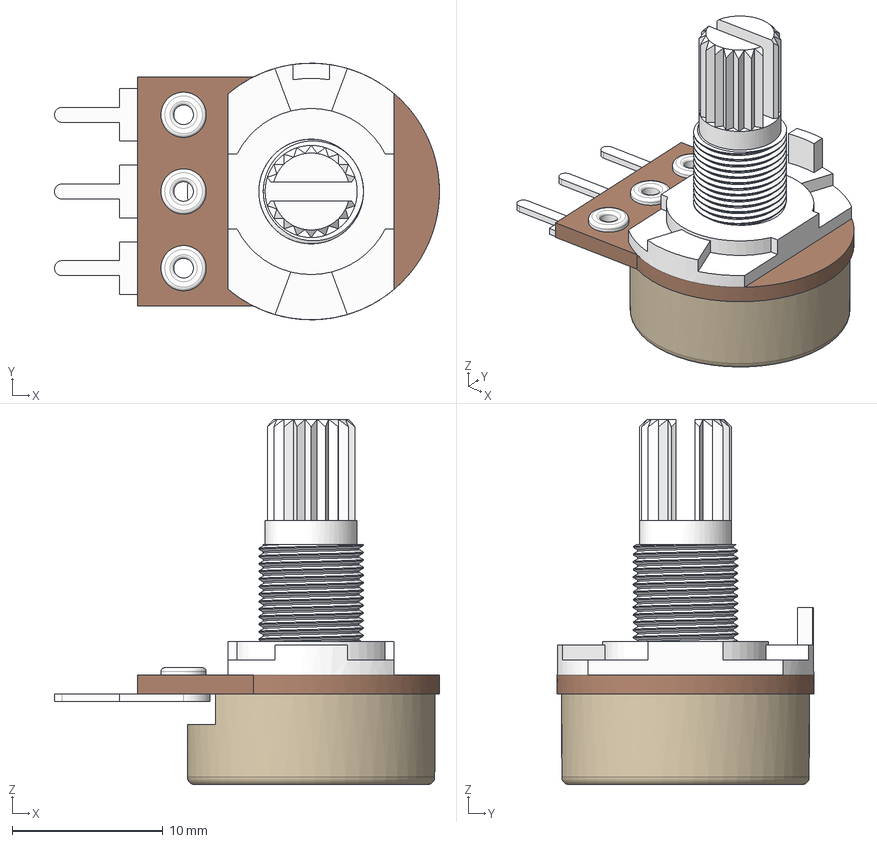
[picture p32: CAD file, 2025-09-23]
KiCad-Libraries/POT10K.step
25.5 x 17.0 x 24.2 mm

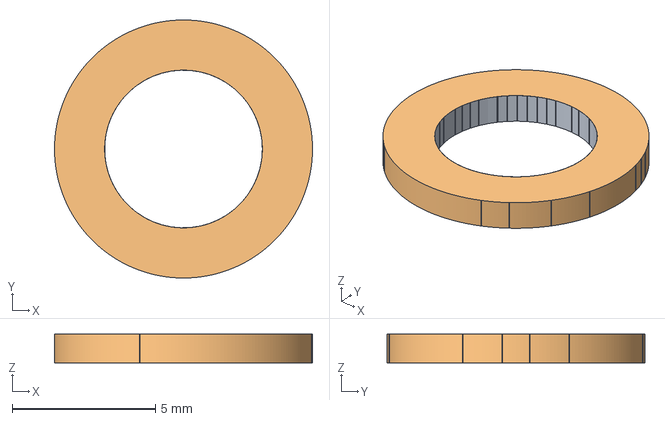
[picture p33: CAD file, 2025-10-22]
Prototipos/Diseños 3D/Arandela/Arandela.FCStd
9.00 x 9.00 x 1.00 mm
Cuerpo
Cuerpo (Meshed)

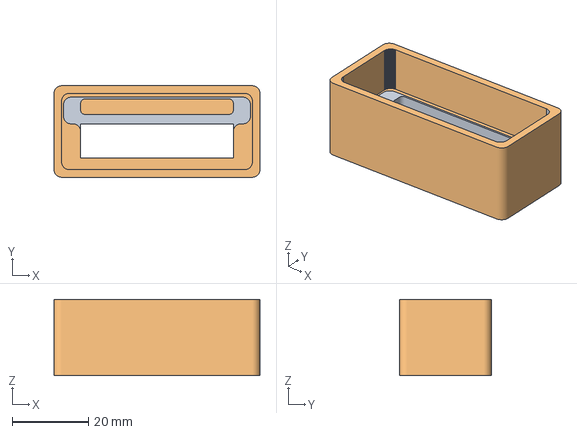
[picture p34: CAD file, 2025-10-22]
Prototipos/Diseños 3D/Carcasa Conector/Carcasa.FCStd
54.0 x 24.0 x 20.0 mm
Cuerpo
Fillet004 (Meshed)

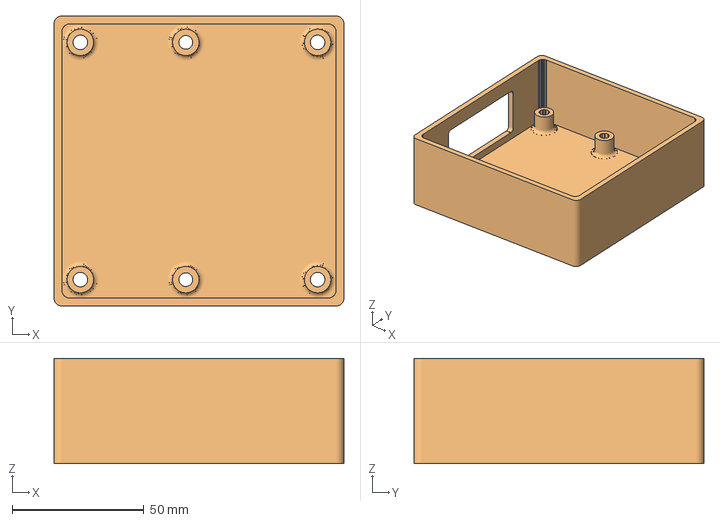
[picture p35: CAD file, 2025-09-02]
Prototipos/Diseños 3D/Gabinete Chico/Gabinete Chico 2.0.FCStd
110.0 x 110.0 x 40.0 mm
Cuerpo
Cuerpo (Meshed)

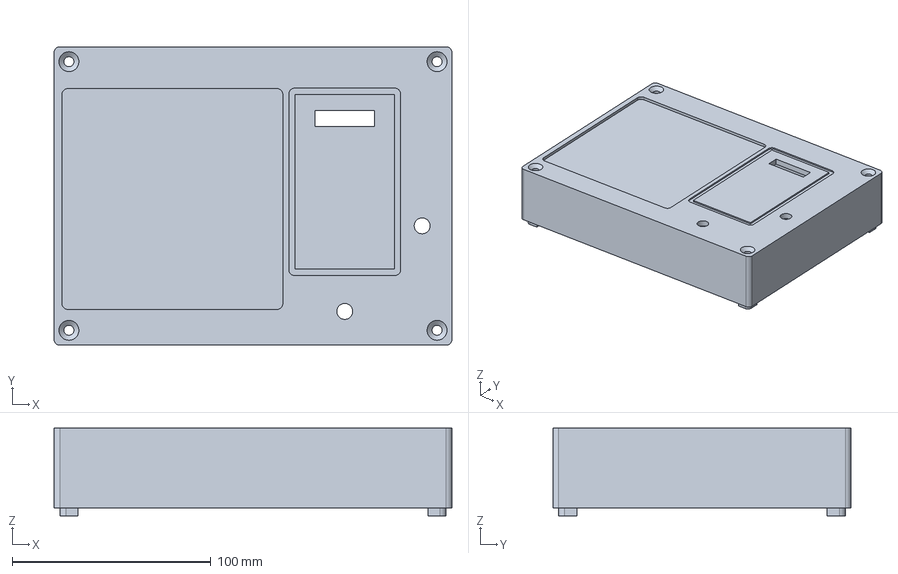
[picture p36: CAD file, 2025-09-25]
Prototipos/Diseños 3D/Gabinete Grande/Gabine Grande Superficie 2.0.FCStd
200.0 x 150.0 x 44.0 mm

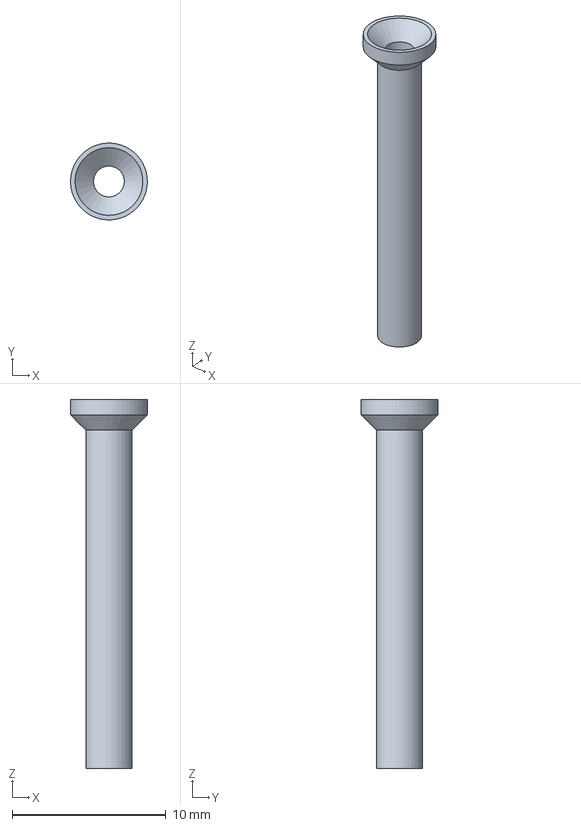
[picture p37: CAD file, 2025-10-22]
Prototipos/Diseños 3D/Test Point/Test point.FCStd
5.00 x 5.00 x 24.0 mm

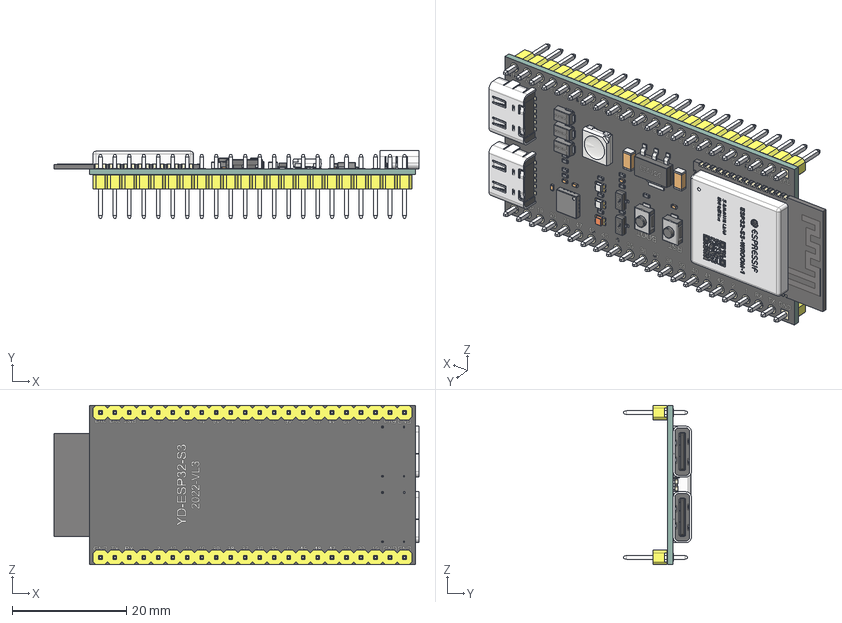
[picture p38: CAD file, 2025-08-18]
KiCad-Libraries/YD-ESP32-S3 v34.step
64.0 x 11.9 x 28.0 mm
PCB
ESP-S3-WROOM_via v3 x 26
ESP32-S3-WROOM_shell v11
ESP32-S3-WROOM_body v12
ESP-S3-WROOM_via v3(镜像) x 14
USB Connector Type C female 6pin x 2
DO220AA x 3
WS2812B
Light
Anode Bottom
Cathode Bottom
Anode
Cathode
Base
Light_1
Anode Bottom_1
Cathode Bottom_1
Anode_1
Cathode_1
Base_1
Light_2
Anode Bottom_2
Cathode Bottom_2
Anode_2
Cathode_2
Base_2
SOT-223
SOT-23 x 2
3x4x2mm - 2 Pad x 2
22way PCB Header x 2

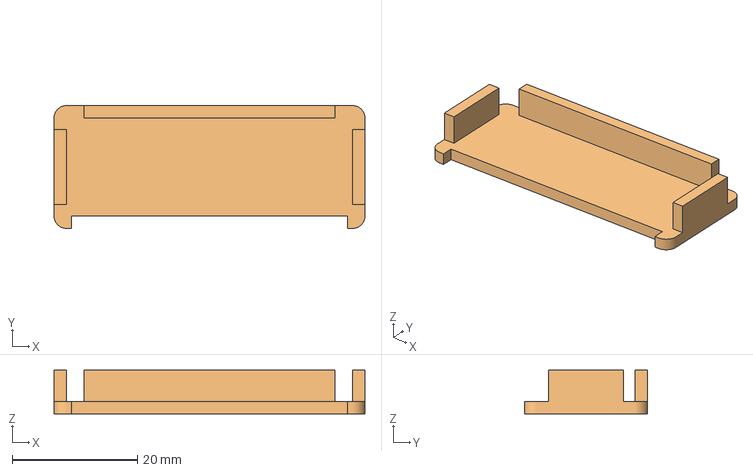
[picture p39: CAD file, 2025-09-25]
Prototipos/Diseños 3D/Carcasa Conector/Tapa carcasa.FCStd
49.6 x 19.6 x 7.00 mm
Cuerpo
Cuerpo (Meshed)

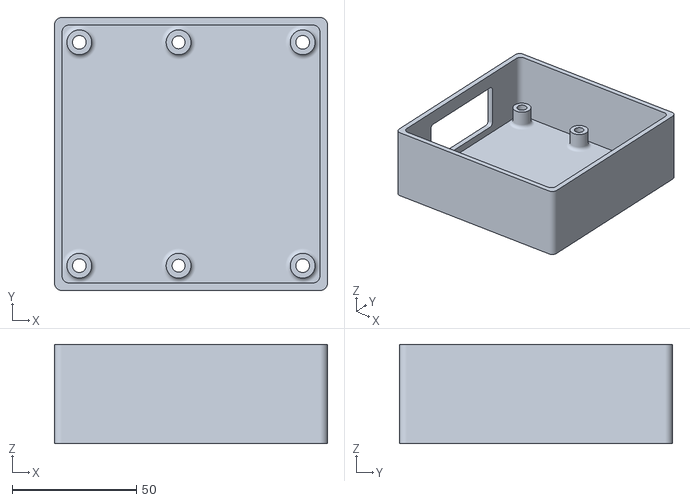
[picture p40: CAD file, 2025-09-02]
Prototipos/Diseños 3D/Gabinete Chico/Gabinete chico.stl
110.0 x 110.0 x 40.0

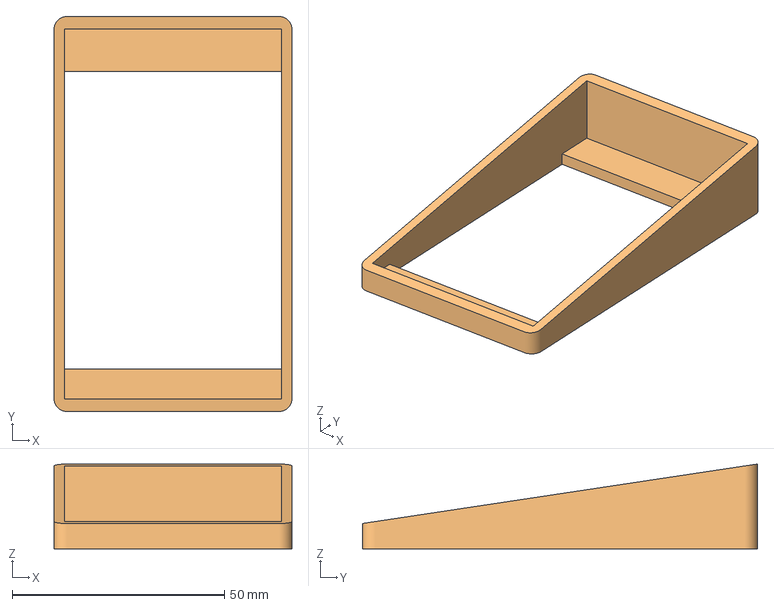
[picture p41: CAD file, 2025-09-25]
Prototipos/Diseños 3D/Gabinete Grande/Angulo Pantalla.FCStd
56.0 x 93.0 x 20.0 mm
Cuerpo
Fillet (Meshed)

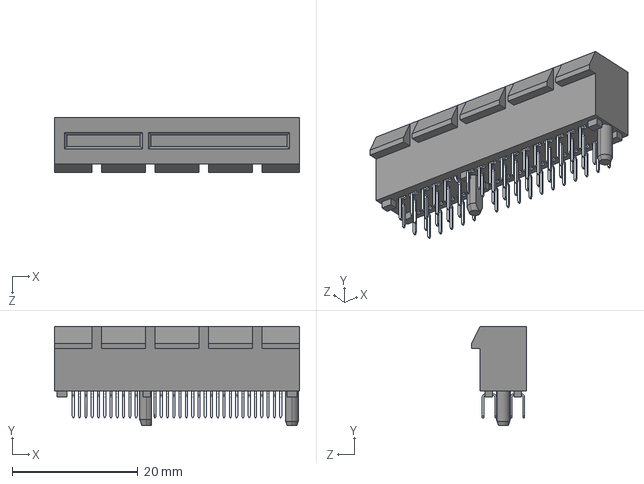
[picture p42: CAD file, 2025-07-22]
KiCad-Libraries/PCIe_x4_male.step
39.0 x 15.8 x 8.80 mm

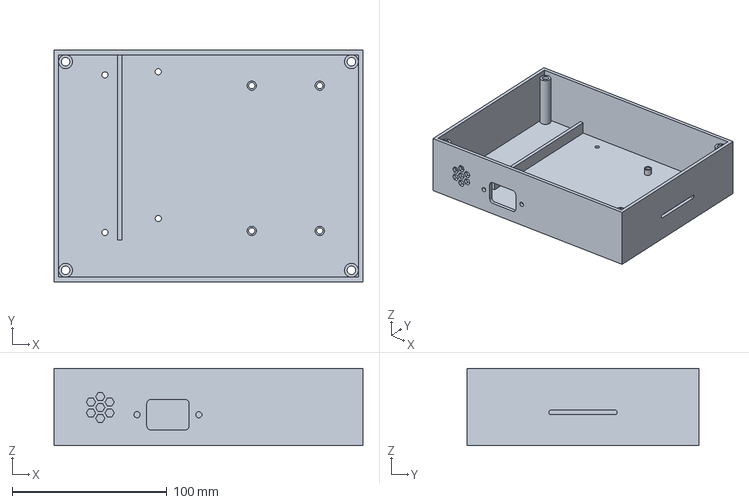
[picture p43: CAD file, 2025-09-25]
Prototipos/Diseños 3D/Gabinete Grande/Gabine Grande Base 2.0.FCStd
200.0 x 150.0 x 50.0 mm

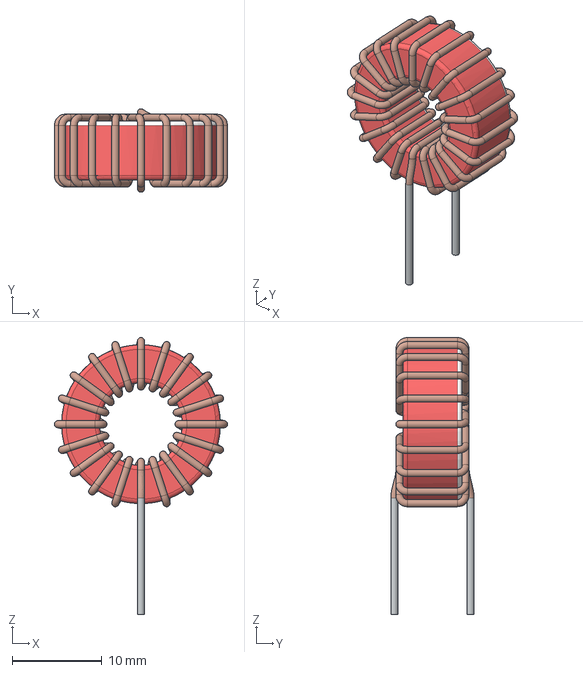
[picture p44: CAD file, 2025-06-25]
KiCad-Libraries/inductor_toroidal.stp
19.3 x 9.30 x 30.9 mm
Turns
Core-T68A

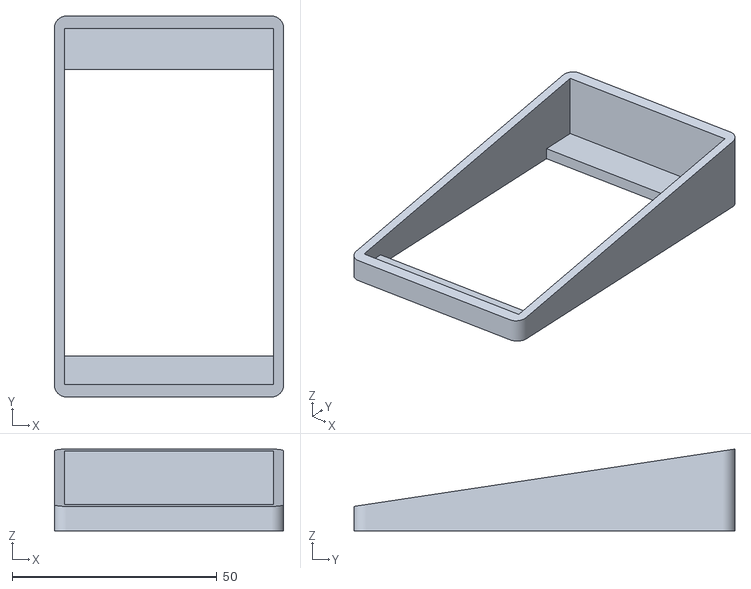
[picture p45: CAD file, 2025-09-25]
Prototipos/Diseños 3D/Gabinete Grande/Angulo.stl
56.0 x 93.0 x 20.0

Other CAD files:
KiCad-Libraries/RV09AF-40-20K-B10K--3DModel-STEP-510211.STEP
Prototipos/Diseños 3D/Gabinete Grande/Gabinete grande superficie.stl
KiCad-Libraries/MOC3021.STEP
Prototipos/Diseños 3D/Gabinete Grande/Gabinete grande base.stl
KiCad-Libraries/BT137-600E,127.stp
KiCad-Libraries/IRF9540NPBF.step
KiCad-Libraries/IRLML6344.step
KiCad-Libraries/MOC3021.step
Prototipos/Diseños 3D/Arandela/Arandela.stl
Prototipos/Diseños 3D/Carcasa Conector/Carcasa.stl
Prototipos/Diseños 3D/Carcasa Conector/TapaCarcasa.stl
Prototipos/Diseños 3D/Test Point/Testpoint.stl

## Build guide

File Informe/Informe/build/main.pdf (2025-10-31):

UNIVERSIDAD TECNOLOGICA ´ | NACIONAL

## Facultad Regional San Francisco

## Ingeniería Electronica ´

SISTEMA DIDACTICO ´ | MODULAR PARA LA
EXPERIMENTACION EN ´ | ELECTRONICA DE ´

## POTENCIA

Autores:
Alesandria, Alejo Samuel
Cignetti, Mateo Antonio
Galliano, Ignacio

Docente:
Ing. Musso, Daniel

Tutores:
Ing. Pipino, Hugo
Ing. Bossio, Jorge

Fecha:

### 7 de noviembre de 2025

PROYECTO FINAL Alesandria, Alejo S. – Cignetti, Mateo A. – Galliano, Ignacio

## Agradecimientos

Queremos expresar nuestro mas profundo agradecimiento a nuestras familias, parejas y amigos, por su ´
comprension, acompa ´ | namiento y aliento incondicional durante todo este camino. ˜
A nuestros tutores, Hugo Pipino y Jorge Bossio, por su incansable colaboracion, orientaci ´ | on y compro- ´
miso a lo largo de todo el proyecto.
A los docentes y no docentes de la institucion, por su constante apoyo y predisposici ´ | on. ´
Finalmente, a Jaies Innovation, de Alejandro Juarez, por su valioso asesoramiento y la prestaci ´ | on de ´
servicios en impresiones 3D, que fueron fundamentales para el desarrollo de nuestro trabajo.

I

## Resumen

En la catedra Electr ´ | onica de Potencia de Ingenier ´ | ía Electronica es dif ´ | ícil abordar todos los contenidos
del programa, debido al poco tiempo disponible durante el ano acad ˜ | emico. Adem ´ | as, no se dispone de un ´
laboratorio especializado de esta tematica en UTN Facultad Regional San Francisco, provincia de C ´ | ordoba ´
(Argentina). Por ello, surge la necesidad de desarrollar un sistema que permita a alumnos o entusiastas
aprender de forma practica e interactiva, optimizando el proceso educativo en la c ´ | | | atedra. ´
Se propone el desarrollo de un sistema general que permite la observacion de se ´ | nales de entrada y sa- ˜
lida con la ayuda de herramientas externas, como un osciloscopio y un multímetro, así como el ajuste de
parametros en tiempo real. El sistema consta de un gabinete central que provee la alimentaci ´ | | | on y el control ´
de cada modulo. Adem ´ | as, consta de una interfaz de usuario y de tres m ´ | odulos para experimentar con dis- ´
tintos circuitos esenciales de la catedra: un convertidor reductor Buck, un recortador de onda y un inversor ´
de onda cuadrada. El sistema esta dise ´ | nado de tal forma que sea posible y simple su escalabilidad, con la ˜
fabricacion de nuevos m ´ | odulos, como convertidores elevadores, inversores de onda sinusoidal, variadores ´
de frecuencia, entre otros.

Palabras clave: experimentador, aprendizaje, herramienta interactiva, portatil, escalable. ´

II

## ÍNDICE

1. Introduccion´ | 1
2. Meta | 2
3. Descripcion´ | 3
4. Objetivos | 4
5. Justificacion´ | 5
6. Alternativas propuestas | 6
6.2. Contribucion del proyecto | ´ | 6
7. Aspectos de mercado | 7
8. Aspectos financieros | 8
9. Aspectos institucionales | 9
10. Aspectos de impacto ambiental | 10
11. Consideraciones generales | 11
11.1. Alimentacion | ´ | 11
12. Diseno de gabinetes de m ˜ | odulos | 12 ´
13. Modulo convertidor reductor o Buck | 15 ´
13.1. Interaccion del usuario: control y verificaci ´ | on experimental | ´ | 15
13.2. Base teorica | ´ | | 15
13.3. Calculos para el dise ´ | no | ˜ | 19
13.3.1. Ciclo de trabajo maximo | ´ | 20

III

13.3.6. Realimentacion microcontrolador | ´ | 25
13.3.10.Seleccion de carga con Rel ´ | e | ´ | 30
13.3.11.Calculo de disipador para MOSFET de conmutaci ´ | on | ´ | 30
13.4. Simulacion | ´ | | 32
14. Modulo recortador de onda | 33 ´
14.1. Interaccion del usuario: control y verificaci ´ | on experimental | ´ | 34
14.2. Base teorica | ´ | | 34
14.3. Calculos e implementaci ´ | on | ´ | 37
14.3.1. Rama RC de control analogico | ´ | 37
14.3.4. Driver de rele | ´ | | 42
14.4. Disipacion de potencia en TRIAC | ´ | | 44
14.5. Simulacion | ´ | | 45
15. Modulo inversor de onda cuadrada | 46 ´
15.1. Interaccion del usuario: control y verificaci ´ | on experimental | ´ | 47
15.2. Descripcion de funcionamiento de un oscilador 555 | ´ | | 47
15.3. Descripcion de funcionamiento de un inversor de medio puente | ´ | | 48
15.4. Calculos | ´ | 51
15.4.1. Temporizador 555 configurado como oscilador con ciclo de trabajo del 50 % . . . . 51
15.4.6. Disipacion de potencia en transistores | ´ | 55
15.5. Simulacion | ´ | 55
16. Desarrollo de Hardware | 56

IV

16.2. Diseno de PCBs finales | ˜ | 57
17. Desarrollo de Software | 63
17.2.3. Module Manager - Gestor de modulos | ´ | 64
17.3. Diseno de interfaz de usuario | ˜ | | 65
17.4. Programacion de m ´ | odulos | ´ | 67
17.4.1. Modulo convertidor Buck | ´ | | 67
17.4.2. Modulo recortador de onda | ´ | | 68
17.4.3. Modulo inversor de onda cuadrada | ´ | | 68
18. Escalabilidad del proyecto | 69
18.1. Guía para agregar un nuevo modulo | ´ | 69
18.1.1. Diseno del hardware | ˜ | | 69
18.1.3. Registro del modulo en el sistema | ´ | 71
19. Resultados del proyecto | 71
19.2. Modulo convertidor reductor o Buck | ´ | | 72
19.3. Modulo recortador de onda | ´ | | 77
19.4. Modulo inversor de onda cuadrada | ´ | | 80
20. Conclusion´ | 83
21. Apendice ´ | 84
REFERENCIAS | 91

V

## 1. Introduccion´

La electronica de potencia es una disciplina que combina tres pilares fundamentales: la energ ´ | ía, la
electronica y el control. Esta integraci ´ | on permite no solo transformar y gestionar la energ ´ | ía de forma eficien-
te, sino tambien implementar estrategias inteligentes para adaptarla a distintas aplicaciones. En este contexto ´
el control se encarga tanto del comportamiento del regimen permanente como de las caracter ´ | ísticas dinami- ´
cas de los sistemas en lazo cerrado; por otro lado, la energía involucra equipos de potencia estatica y rotativa ´
o giratoria, para la generacion, transmisi ´ | on y distribuci ´ | on de la misma; por ´ | ultimo, la electr ´ | onica se ocupa de ´
los dispositivos y circuitos de estado solido requeridos en el procesamiento de se ´ | nales para cumplir con los ˜
objetivos de control deseados. Por ende, la electronica de potencia puede ser definida como “la aplicaci ´ | on´
de la electronica de estado s ´ | olido para el control y la conversi ´ | on de la energ ´ | ía electrica”, (Rashid, 2015). ´

El avance en la tecnología de semiconductores de potencia ha ampliado enormemente las capacidades
de conmutacion, eficiencia y miniaturizaci ´ | on de los sistemas electr ´ | onicos; tambi ´ | en debido al uso de al- ´
tas frecuencias para la implementacion de los sistemas. Asimismo, el desarrollo de la tecnolog ´ | ía de los
microprocesadores-microcomputadoras tiene un gran impacto sobre el control y la síntesis de las estrategias de control para los dispositivos semiconductores de potencia, (Rashid, 2015).
Sin embargo, a pesar del amplio protagonismo de la electronica de potencia en m ´ | ultiples sectores, como ´
la industria, el transporte, o la automatizacion; y en la vida cotidiana, como electrodom ´ | esticos conven- ´
cionales, su ensenanza contin ˜ | ua enfrentando importantes desaf ´ | íos. Entre ellos, se destacan la dificultad de
acceder a laboratorios completamente equipados, los costos elevados de ciertos componentes y, sobre todo,
la escasez de tiempo en los programas academicos para abordar un contenido tan amplio y pr ´ | actico. ´

Planteado este escenario, surge la necesidad de desarrollar una herramienta accesible, segura y adaptable que facilite significativamente las dificultades previamente mencionadas. En el presente proyecto se propone el desarrollo de un equipamiento didactico que permite a los estudiantes experimentar y fortalecer los ´
principios teoricos mediante la pr ´ | actica, facilitando el aprendizaje activo. Esta experiencia pr ´ | actica es vital ´
para el desarrollo de habilidades críticas, resolver problemas complejos y prepararse para los desafíos del mundo real.

A su vez, se preve que el sistema cuente con un manual de usuario que explique como utilizar cada ´
modulo y una gu ´ | ía practica que oriente sobre los par ´ | ametros a modificar y los efectos a analizar. Con este ´
enfoque, se espera que los usuarios desarrollen una comprension profunda y tangible de los principios de la ´
materia. Uno de los beneficios del diseno modular es que, en el futuro, se podr ˜ | an incorporar expansiones o ´
modulos personalizados seg ´ | un las necesidades del usuario o avances tecnol ´ | ogicos; de este modo, el proyecto ´
queda abierto a mejoras continuas y a la adaptacion a nuevas ´ | areas de estudio de la electr ´ | onica. ´

## 2. Meta

Este proyecto tiene como meta facilitar el aprendizaje practico de electr ´ | onica de potencia mediante un ´
sistema didactico modular que permita la experimentaci ´ | on directa y el desarrollo de competencias a trav ´ | es´
de modulos especializados y material te ´ | orico complementario. ´

## 3. Descripcion´

El proyecto consiste en el diseno y construcci ˜ | on de un sistema did ´ | actico modular orientado a la ense ´ | nanza ˜
y aprendizaje de la electronica de potencia. Est ´ | a destinado a estudiantes y entusiastas que deseen experimen- ´
tar con diferentes configuraciones de circuitos, tales como rectificadores, inversores, convertidores DC-DC, entre otros.

El sistema es comandado por un gabinete central que cuenta con una fuente de tension de 12 V, un ´ transformador de 220 V a 48 V, una PCB de control general con un microcontrolador ESP32-S3 y una interfaz compuesta por una pantalla y un encoder rotativo. El gabinete posee un cable con conector PCIe x4
hembra que permite la conexion de diferentes m ´ | odulos funcionales. ´
Se contempla el desarrollo de tres modulos funcionales. El dise ´ | no modular elegido facilita la expansi ˜ | on´
futura del sistema, permitiendo incorporar nuevos modulos personalizados conforme a las necesidades de ´
los usuarios o los avances tecnologicos. As ´ | í, el proyecto se concibe como una plataforma abierta, adaptable
y en constante evolucion. ´

Los modulos desarrollados en este proyecto son los siguientes: ´

Recortador de onda: regula la potencia entregada a la carga mediante el uso de un tiristor, recortando la onda de tension. ´
Convertidor Buck: logra una tension de salida menor a la tensi ´ | on de entrada sin prescindir de eficien- ´
cia.
Inversor de onda cuadrada: transfiere potencia desde una fuente de continua a una carga de alterna.
El sistema en su totalidad permite la observacion de se ´ | nales de entrada y salida con la ayuda de herra- ˜
mientas externas, así como el ajuste de parametros en tiempo real, lo que posibilita un aprendizaje pr ´ | actico ´
e interactivo. A traves de estas interacciones, se busca que los usuarios comprendan de forma tangible los ´ principios fundamentales de la electronica de potencia. ´
En el desarrollo del trabajo se implemento la metodolog ´ | ía agil Scrum, entendida como un marco de ´
trabajo ligero que permite generar valor a traves de soluciones adaptativas frente a problemas complejos, ´
(Schwaber & Sutherland, 2020). El trabajo se dividio en ´ | sprints, permitiendo una planificacion incremental ´
y entregas periodicas. Adem ´ | as, se utiliz ´ | o la funci ´ | on Proyectos de GitHub para gestionar una pizarra de ´
tareas, organizando el flujo de trabajo en columnas: backlog, ready, in progress, in review y done. Esto
facilito el seguimiento del avance, la asignaci ´ | on de responsabilidades y la colaboraci ´ | on entre los integrantes ´
del equipo.

## 4. Objetivos

Con el fin de lograr un sistema optimo que cumpla con un correcto funcionamiento y fiabilidad, se ´ plantearon objetivos para establecer el rumbo del proyecto, definiendo de forma clara y precisa lo que se pretende alcanzar.

### 4.1. Objetivo General

Disenar un sistema did ˜ | actico modular para la experimentaci ´ | on de electr ´ | onica de potencia, con el fin ´
de facilitar el aprendizaje practico mediante el uso de m ´ | odulos especializados y material te ´ | orico com- ´
plementario; enfatizando la simplicidad de uso, seguridad y adaptabilidad para futuros desarrollos.

### 4.2. Objetivos Específicos

1. Seleccionar los modulos a implementar en el sistema did ´ | actico. ´
2. Desarrollar los circuitos y placas de los modulos, considerando aspectos de potencia y disipaci ´ | on de ´
calor.
3. Disenar los m ˜ | odulos con la intenci ´ | on de ser f ´ | acilmente conectables e intercambiables. ´
4. Seleccionar los componentes y materiales necesarios para la construccion de los m ´ | odulos. ´
5. Disenar los gabinetes y la estructura del sistema para facilitar su impresi ˜ | on en filamento 3D. ´
6. Adaptar el sistema para futuras expansiones y mejoras.
7. Validar el correcto funcionamiento de los modulos mediante pruebas y ajustes. ´
8. Disenar una interfaz de usuario intuitiva y accesible. ˜
9. Asegurar la seguridad del sistema y de los usuarios.
10. Evaluar el funcionamiento del sistema en su totalidad.
11. Elaborar un manual de usuario que sirva como complemento teorico y facilite la puesta en marcha del ´ sistema.
12. Garantizar el facil mantenimiento y reparaci ´ | on del sistema, en caso de ser necesario. ´
13. Validar el funcionamiento del sistema a traves de pruebas con usuarios finales. ´

## 5. Justificacion´

La motivacion principal del proyecto surge de la necesidad de contar con herramientas accesibles, seguras ´ y eficaces para el aprendizaje de la electronica de potencia, especialmente en contextos donde no se dispone ´ de laboratorios especializados o se cuenta con tiempo limitado para el dictado de la asignatura. En particular,
busca dar respuesta a una problematica planteada por la c ´ | atedra de Electr ´ | onica de Potencia: la dificultad para ´
abordar todos los contenidos del programa en el tiempo disponible durante el ano acad ˜ | emico. ´

El desarrollo del sistema didactico responde a la necesidad de mejorar los tiempos de aprendizaje y ´
ensenanza, permitiendo experimentar de manera te ˜ | orico-pr ´ | actica y activa. Esta soluci ´ | on fue consultada con ´
el titular de la catedra, quien remarc ´ | o que la falta de herramientas adecuadas dificulta el desarrollo del ´
contenido practico dentro de la planificaci ´ | on de la materia. Por ello, el proyecto busca facilitar la integraci ´ | on´
de la teoría y la practica, optimizando el proceso educativo en electr ´ | onica de potencia. ´
Una de las principales ventajas del sistema es su caracter escalable, lo que mejora a ´ | un m ´ | as las posibili- ´
dades de aprendizaje, ya que permite agregar nuevos modulos o adaptar los ya existentes sin necesidad de ´ reemplazar el dispositivo. Esto amplía su vida util y asegura su vigencia frente a las constantes evoluciones ´ del area. ´
Otra característica del sistema es el diseno del circuito de cada m ˜ | odulo en bloques, permitiendo al usuario ´
visualizar las distintas etapas de cada modulo. De esta forma, se facilita la comprensi ´ | on y aprendizaje de ´
cada circuito.

Por otra parte, el dispositivo fue desarrollado íntegramente con componentes convencionales y de amplia disponibilidad, con el objetivo de reducir costos y mejorar la posibilidad de mantenimiento en caso de ser
necesario. Ademas, cuenta con un manual de usuario que sirve como gu ´ | | | ía para utilizar de forma segura y
correcta cada uno de los modulos, y tambi ´ | en incluye preguntas orientadoras para incentivar la reflexi ´ | on y el ´
estudio autonomo del tema. ´

De este modo, el proyecto contribuye al fortalecimiento de la infraestructura educativa, favoreciendo la
formacion de profesionales con competencias pr ´ | acticas, fomenta la innovaci ´ | on en el aula y promueve una ´
mayor integracion entre teor ´ | ía y practica en un entorno accesible, seguro y sostenible, consolidando as ´ | í la
calidad de ensenanza en electr ˜ | onica de potencia. ´

## 6. Alternativas propuestas

### 6.1. Antecedentes

Existen diversos trabajos relacionados a la mejora de la ensenanza de electr ˜ | onica de potencia mediante ´
el uso de dispositivos didacticos. Por ejemplo, el trabajo “M ´ | odulos Did ´ | acticos de Electr ´ | onica de Potencia ´
para el control de maquinas de corriente directa”, (Cordeiro et al., 2009), desarrolla m ´ | | | odulos que permiten ´
estudiar características y tecnicas de control de motores el ´ | ectricos. ´
De manera complementaria, el “Desarrollo de un inversor monofasico did ´ | actico”, (Sandoval et al., 2006), ´
se orienta al diseno de un dispositivo enfocado en una sola rama de la electr ˜ | onica de potencia: la conversi ´ | on´
de corriente continua en corriente alterna. En la misma línea, se encuentra el trabajo “Desarrollo de una Pla-
taforma Didactica para Convertidores de Electr ´ | onica de Potencia Flexibles”, (França et al., 2022), propone ´
un sistema que facilite la comprension y pr ´ | actica de la conversi ´ | on de energ ´ | ía a traves de convertidores de ´
distintas topologías, como el convertidor de puente completo.
Finalmente, otro trabajo que presenta una alternativa didactica, “Dise ´ | no e Implementaci ˜ | on de un Pro- ´
totipo de Tablero Didactico Modular para el Laboratorio de Electr ´ | | onica 3”, (Gonz ´ | alez, 2023), tiene como ´
objetivo el diseno de un tablero did ˜ | actico que facilite la labor del docente y favorezca la comprensi ´ | on de los ´
estudiantes, con un enfoque particular a la programacion. Este trabajo es el ´ | unico de los mencionados que ´
fue entregado como proyecto de graduacion. ´

### 6.2. Contribucion del proyecto ´

Los trabajos mencionados ponen de manifiesto la necesidad de contar con un dispositivo didactico que ´
aproxime los contenidos teoricos a la pr ´ | actica, favoreciendo el trabajo docente, la comprensi ´ | on de los alum- ´
nos y con capacidad de expansion a distintos contextos acad ´ | emicos. Sin embargo, muchos de estos desarro- ´
llos unicamente se centran en el desarrollo de aplicaciones espec ´ | íficas sin abarcar otras tematicas de inter ´ | es. ´
Ademas, cabe destacar que en la regi ´ | on no se dispone de ninguna soluci ´ | on o dispositivo similar. ´

En este contexto, el proyecto busca aportar una alternativa modular y accesible, que facilite la ensenanza, ˜
y que tambien se mantenga vigente frente a la evoluci ´ | on tecnol ´ | ogica. ´

## 7. Aspectos de mercado

En la actualidad existen diversos dispositivos y laboratorios portatiles orientados a aplicaciones did ´ | acti- ´
cas y de aprendizaje en electronica de potencia. Un ejemplo es el desarrollo de K&H PE-5000 Power Elec- ´
tronics Training System, (K&H, 2025), que consiste en 28 modulos experimentales, un motor trif ´ | asico de ´
jaula de ardilla, cargas diversas, control y dispositivos de medicion. Dentro de los m ´ | odulos incluye rectifi- ´
cadores monofasicos, trif ´ | asicos, inversores, entre otros. ´

En la misma línea que el sistema anterior se encuentra el ofrecido por GW Instek, PTS-3100 (GW Instek,
2021), que incorpora modulos como fuentes y cargas de DC y AC. Adem ´ | as, incluye un osciloscopio para ´
poder realizar las mediciones de las experiencias. Otra solucion destacada son los productos de la serie ´
LabVolt de Festo Didactic, (Festo Didactic, 2025), los cuales abarcan modulos para aprender sobre teor ´ | ía
fundamental de corriente alterna, transistores de potencia y tiristores, comunicacion anal ´ | ogica, entre otros. ´

Finalmente, se encuentran los modulos de entrenamiento ofrecidos por Eplimin S.A.C, (Eplimin S.A.C, ´
2025), orientados a electronica digital, electr ´ | onica de potencia y m ´ | odulos anal ´ | ogicos, cada uno acompa ´ | nado ˜
de un manual de usuario electronico. ´
Cabe senalar que estas opciones comerciales no presentan precios en sus p ˜ | aginas oficiales, dado que se ´
fabrican bajo pedido y estan destinadas principalmente a instituciones educativas y centros de formaci ´ | on´
tecnica. ´

## 8. Aspectos financieros

La gestion eficiente de los recursos financieros es un aspecto cr ´ | | | ítico en el desarrollo de proyectos, espe-
cialmente cuando se involucran componentes especializados y procesos de fabricacion personalizados. La ´ Tabla 1 presenta un desglose detallado de los gastos del proyecto, convertidos al valor de venta del dolar del ´
Banco de la Nacion Argentina en cada fecha. Esta informaci ´ | on permite un seguimiento preciso de los cos- ´
tos, sirviendo como base para evaluar la viabilidad economica del proyecto y optimizar futuras asignaciones ´ presupuestarias.

Tabla 1: Gastos del proyecto

Fecha | Descripcion | Costo ´
08/04/2025 | Componentes electronicos varios para placa experimental perforada ´ | | 19,16 USD
23/06/2025 | Componentes electronicos varios para PCB prototipo ´ | | 90,51 USD
02/07/2025 | Placa de desarrollo ESP32-S3 N16R8 | 6,88 USD
16/07/2025 | Pantalla TFT LCD 2,8 | ′′ | 20,88 USD
17/07/2025 | Placas adaptador M2 a PCIe X4 | 6,43 USD
22/07/2025 | Componentes electronicos varios para gabinete central ´ | | 23,53 USD
13/08/2025 | Transformador 220 V/48 V 50 VA | 41,51 USD
19/08/2025 | Impresion 3D #1 ´ | | 3,82 USD
04/09/2025 | Impresion 3D #2 y #3 ´ | | 5,33 USD
22/09/2025 | Fabricacion de PCBs m ´ | odulos en JLCPCB ´ | 40,55 USD
23/09/2025 | Impresion 3D #4 ´ | | 6,00 USD
N/A | Insumos varios | | 23,56 USD
Total | | | 288,16 USD

## 9. Aspectos institucionales

El presente proyecto no se encuentra enmarcado en ninguna institucion educativa, empresarial ni guber- ´ namental, sino que fue desarrollado de manera independiente con recursos propios. Su ejecucion responde ´ exclusivamente a los objetivos planteados, sin el patrocinio ni la participacion de organismos externos. ´

## 10. Aspectos de impacto ambiental

Se denomina impacto ambiental a todo cambio que tiene lugar en el medio ambiente o en alguno de sus componentes, ya sea perjudicial o beneficioso, como resultado de una accion, conjunto de acciones o ´ actividad. En este contexto, se considera que existe un impacto ambiental cuando existe una diferencia entre
la situacion del medio ambiente futuro producto de la realizaci ´ | on de un proyecto, y la situaci ´ | on del medio ´
ambiente futuro sin este, (Chaer Ingenier ´ | ía Ambiental, 2020).

En el presente proyecto, uno de los impactos ambientales negativos de mayor consideracion es producto ´ de las impresiones 3D, donde en lugar de utilizar un filamento biodegradable como lo es el PLA (acido ´ polilactico), se utiliza el PETG (tereftalato de polietileno glicol), el cual es un filamento que presenta mayor ´
resistencia mecanica, durabilidad y flexibilidad, adem ´ | as soporta mayores temperaturas antes de superar el ´
umbral de deformacion t ´ | ermica. Si bien no es biodegradable como el PLA, el mismo es reciclable al ´ | 100 %,
(TP3D, 2023).
Tambien se emplea en la elaboraci ´ | on del sistema un policarbonato transparente, utilizado como tapa de ´
cada gabinete individual de los modulos. Este cumple la funci ´ | on de impedir que el usuario acceda con las ´
manos a la PCB, y por otro lado, senalar los puntos de prueba disponibles dentro del m ˜ | odulo en uso. Es ´
de destacar que el material fue cedido por UTN Facultad Regional San Francisco en forma de un retazo sobrante, lo que permite su reutilizacion y contribuye a reducir el impacto ambiental asociado al desecho de ´ plasticos. ´
Ademas, se hizo uso de un transformador para reducir la tensi ´ | on de l ´ | ínea domestica, si bien la fabricaci ´ | on´
no esta a cargo del grupo de trabajo, debe considerarse como un impacto ambiental total dentro del proyecto. ´ El proceso de manufactura del transformador implica el consumo de materias primas, como el cobre y acero,
ademas de la energ ´ | ía necesaria para las maquinarias utilizadas en el proceso. No obstante, al tratarse de un
componente estandar y de larga vida ´ | util, el impacto ambiental relacionado al mismo puede verse atenuado ´
en el tiempo y reducido en relacion al ciclo de vida del dispositivo completo. ´
El impacto ambiental respecto a la elaboracion de las PCB se limita a la fabricaci ´ | on y transporte de ´
los componentes desde la fabrica al proveedor, y desde el mismo a la ciudad de destino. Considerando el ´ consumo del dispositivo, se tiene la fuente de alimentacion de corriente continua y el transformador. La ´
primera tiene un consumo maximo dependiendo de los m ´ | odulos, siendo que los mismos se desarrollaron ´
para 12 V y 3 A maximos, dando as ´ | í un consumo maximo de ´ | 36W. El transformador utilizado es de 50 VA
con una potencia activa maxima de ´ | 48W. Para estimar el impacto energetico asociado al uso del dispositivo, ´
se considera la potencia maxima con un ´ | 25 % adicional para abarcar el rendimiento de las etapas de potencia
y cualquier perdida no considerada. ´
Ptotal = (36W + 48W)1, 25 = 105W | | | (1)

Se trata de un consumo reducido, incluso menor que el de una computadora de escritorio en funcionamiento, lo que se traduce en una menor demanda energetica y, en consecuencia, en un impacto ambiental ´ reducido.

## 11. Consideraciones generales

Se comienza el desarrollo del proyecto con el diseno del gabinete central. El mismo debe ser capaz de ˜
alimentar los modulos, con ´ | 12 V de corriente continua y 48 V de corriente alterna. Ademas, debe contar con ´
el microcontrolador encargado de manejar el sistema completo y los conectores para la comunicacion con ´
los modulos y con los perif ´ | ericos necesarios para la interfaz de usuario. ´

### 11.1. Alimentacion´

Para la alimentacion, se emplea una fuente conmutada de ´ | 12 V de corriente continua, 5 A maximo de ´
salida (60W), con entrada 220 V de corriente alterna. Ademas, se dispone de un transformador de corriente ´
alterna de entrada 220 V y salida 48 V, 1 A maximo de salida ( ´ | 48 VA).

### 11.2. Control

Para el control del sistema en general se utiliza el microcontrolador Espressif ESP32-S3, (Espressif Systems, 2025a), por su versatilidad compacta y robustez funcional: dispone de una gran cantidad de entradas/salidas configurables y dos conversores analogico-digitales de 12 bits. ´

### 11.3. Interfaz de usuario

Para la interfaz de usuario, se utiliza un display LCD TFT de 2,8

′′ con comunicacion SPI y resoluci ´ | on´

de 240 × 320 píxeles; y un encoder rotativo para navegacion. ´

### 11.4. Circuito

En la figura Figura 1, se observa un diagrama en bloque del circuito disenado. Para la comunicaci ˜ | on´
entre el gabinete central y los modulos, se utiliza un cable plano soldado directamente a la placa del gabinete ´ central, con un conector PCIe x4 hembra en el otro extremo.

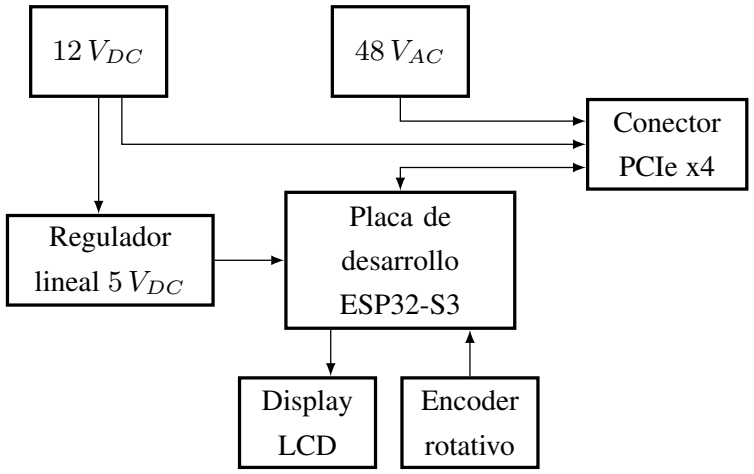
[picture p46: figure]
12 VDC; 48 VAC; Conector; PCIe x4; Placa de; desarrollo; ESP32-S3; Display; LCD; Encoder; rotativo; Regulador; lineal 5 VDC

Figura 1: Diagrama en bloques del circuito del gabinete central.

Una vez disenado el circuito de la placa del gabinete central, se procede a dise ˜ | nar los modelos del mismo, ˜
así como de los demas componentes del proyecto. ´
12. Diseno de gabinetes de m ˜ | odulos ´
Para la construccion de los gabinetes de cada m ´ | odulo y del gabinete general del prototipo, se opta por ´
la impresion 3D, ya que esta tecnolog ´ | ía permite fabricarlos a medida con las especificaciones requeridas,
ademas de ofrecer costos accesibles y una r ´ | apida producci ´ | on. Los dise ´ | nos se realizan en FreeCAD (Riegel ˜
et al., 2024), seleccionado por ser un software libre, facil de usar y altamente vers ´ | atil. ´

### 12.1. Gabinete general

El gabinete principal, encargado de controlar todo el sistema, debe tener la capacidad suficiente para
alojar en su interior la fuente de tension de ´ | 12 V de corriente continua, el transformador de 48 V de corriente
alterna y la PCB general de control y distribucion de energ ´ | ía. Ademas, en la superficie debe quedar espacio ´
para ubicar el gabinete individual en prueba, junto con la pantalla interactiva y el encoder rotativo.

En base a estos requerimientos, se disena un gabinete compuesto por dos partes: una inferior (base), ˜
destinada a la fijacion de los elementos de alimentaci ´ | on y control, y una superior, en la cual se instala el ´
display de 2,8

′′ con el encoder, ademas del espacio para apoyar el gabinete individual. ´

Asimismo, se disena un soporte en ˜ | angulo para el display, que cumple la doble funci ´ | on de mejorar su ´
visualizacion y proteger la PCB del mismo. ´

Figura 2: Soporte en angulo para el display. ´

Las dimensiones finales del gabinete son de 20 × 15 cm, con sus piezas unidas mediante tornillos. En la base se realizan todas las perforaciones necesarias para fijar la PCB, la fuente de corriente continua y el transformador de corriente alterna con tornillos Allen de cabeza fresada. Finalmente, en el lateral posterior se
incorpora una rejilla de ventilacion y dos aberturas para instalar un conector macho ´ | interlock y un interruptor
de encendido. En el lateral izquierdo se deja una ventana destinada al paso del cable plano que conecta el gabinete general a los modulos. ´

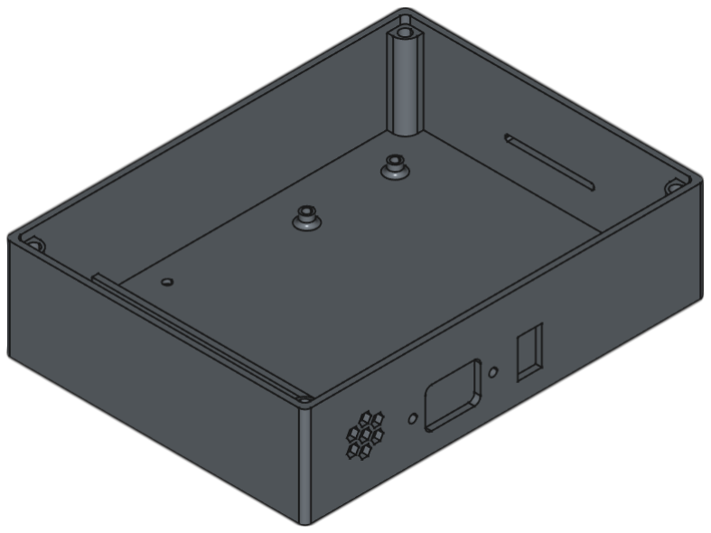
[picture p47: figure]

(a) Base de gabinete general.

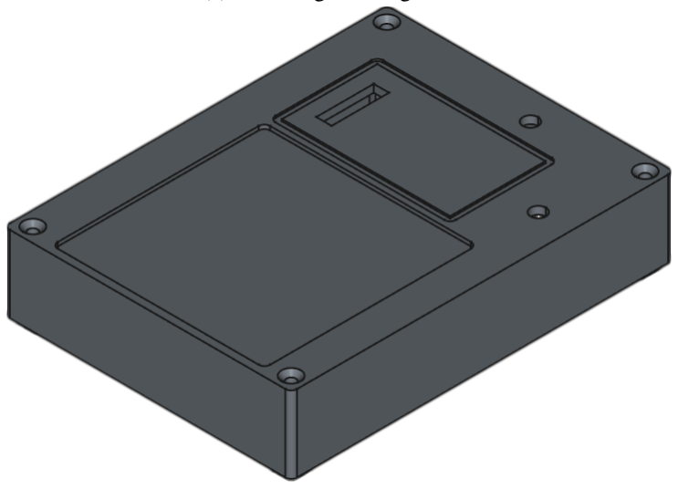
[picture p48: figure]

(b) Tapa superior de gabinete general.

Figura 3: Piezas que componen el gabinete general.

### 12.2. Gabinete individual

El gabinete destinado a cada modulo se concibe inicialmente como una caja cuadrada en la cual pudiera ´ fijarse una placa de circuito impreso (PCB) de 10×10 cm, separada un centímetro del fondo mediante cuatro separadores huecos que permiten el paso de tornillos. En un primer diseno, la caja no contemplaba tapa, lo ˜ que implicaba un contacto directo del usuario con la PCB. Para evitarlo, se incorpora una tapa de acrílico transparente que cubre la totalidad de la superficie superior del gabinete. De esta forma se impide el contacto directo con la electronica, pero al mismo tiempo se mantiene la visibilidad de la placa. No obstante, esta ´
solucion dificulta la realizaci ´ | on de mediciones directas, por lo que se a ´ | nadieron perforaciones en el acr ˜ | ílico,
de tamano suficiente para permitir el ingreso de las puntas de un mult ˜ | ímetro u osciloscopio, sin comprometer
la seguridad del usuario.
Posteriormente se considera que los modulos solo requieren de una PCB de ´ | 10 × 5 cm. Sin embargo, se
decide mantener el diseno original para conservar una l ˜ | ínea de universalidad que brinde libertad al usuario

en el desarrollo de distintos modulos. Para ello, se a ´ | naden dos separadores adicionales que permiten fijar ˜
tambien placas de ´ | 10 × 5 cm por sus cuatro esquinas.
La ultima consideraci ´ | on es la conexi ´ | on de los m ´ | odulos. Se busca una soluci ´ | on que evitara tener que ´
desmontar la PCB para realizar las conexiones. Esto se resuelve disenando el gabinete con una ventana ˜ lateral del tamano exacto del conector, de modo que la PCB pueda alojar el conector en su borde y conectarse ˜ directamente desde el exterior.

Figura 4: Gabinete individual.

### 12.2.1. Conector PCIe x4

El conector PCIe x4 se monta sobre una PCB desde la cual se desprenden los cables correspondientes.
Para su proteccion, se dise ´ | na una caja negra en la que, en su cara frontal, queda accesible el conector; ˜
mientras que en la cara posterior se coloca una tapa con una abertura lo suficientemente amplia para permitir el paso de los cables.

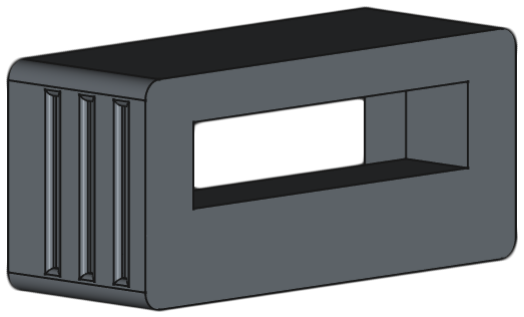
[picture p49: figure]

Figura 5: Carcasa para conector PCIe x4.

## 13. Modulo convertidor reductor o Buck ´

Un convertidor es un circuito electronico que transforma energ ´ | | ía electrica de una forma a otra, ya sea ´
cambiando niveles de tension, corriente o frecuencia. En el caso del Buck, se trata de un tipo espec ´ | ífico de
convertidor DC-DC (Direct Current, corriente continua en espanol) que disminuye la tensi ˜ | on de entrada a ´
una menor en la salida, manteniendo una buena eficiencia gracias a su operacion conmutada. Este conver- ´ tidor funciona mediante el encendido y apagado rapido de un transistor, aprovechando elementos reactivos ´ como inductores y capacitores para almacenar y transferir energía de manera controlada, evitando las perdi- ´ das típicas de los reguladores lineales.
13.1. Interaccion del usuario: control y verificaci ´ | on experimental ´

El usuario puede interactuar con el modulo mediante una interfaz intuitiva que permite seleccionar entre ´
diferentes modos de control, como regulacion autom ´ | atica de tensi ´ | on mediante PID (control proporcional, ´
integrador y derivativo) o ajuste manual del ciclo de trabajo PWM (Pulse Frequency Modulation, modula-
cion por frecuencia de pulso). Adem ´ | as, se puede modificar la frecuencia de conmutaci ´ | on y alternar entre ´
una carga resistiva o inductiva usando el rele integrado. Se dispone de diversos ´ | | | test points a traves de la PCB ´
con el fin de poder realizar pruebas en tiempo real utilizando herramientas de medicion como osciloscopios, ´ multímetros, entre otros.
Las principales senales que se observan en el m ˜ | odulo son: la tensi ´ | on de salida (a trav ´ | es de la cual se ´
puede observar la estabilidad de tension frente a distintas condiciones de carga), la corriente en el inductor ´
y la corriente de carga y descarga del capacitor. A su vez, se permite visualizar la senal de conmutaci ˜ | on´
en el transistor, proporcionando así una experiencia completa para el aprendizaje y la caracterizacion del ´ convertidor Buck.

El objetivo de esto es poner a disposicion del usuario la mayor cantidad de pruebas posibles como, por ´ ejemplo, analizar el efecto que produce una carga inductiva y resistiva sobre el PWM del microcontrolador, o el resultado en el ripple debido al cambio de frecuencia de conmutacion o al PWM. ´

### 13.2. Base teorica ´

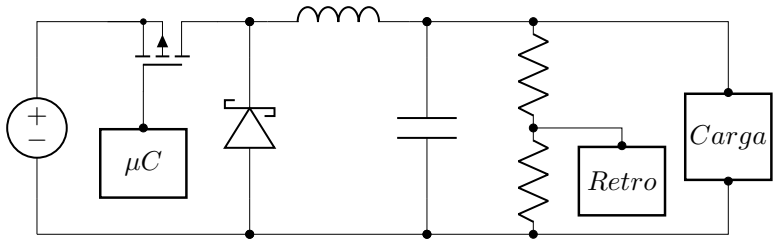
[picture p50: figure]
Carga; Retro

Figura 6: Circuito basico del convertidor Buck. ´

Un convertidor Buck consta de un diodo, un filtro de salida, un circuito de realimentacion y un interruptor ´
al cual se le controla su conmutacion, Figura 6; siendo el objetivo lograr una tensi ´ | on de salida menor a la ´
tension de entrada sin prescindir de eficiencia. ´

El interruptor se encarga de traspasar la potencia, de la entrada a la salida, dependiendo de la velocidad
de conmutacion o del tiempo que se encuentre encendido, la tensi ´ | on en la salida puede aumentar o disminuir, ´
pero manteniendose siempre por debajo de la tensi ´ | on de entrada, o en casos puede alcanzar el valor de la ´
entrada, (Rashid, 2024).

En este tipo de topología de convertidores DC-DC se suele emplear un transistor MOSFET canal p como interruptor en lugar de un MOSFET canal n, debido a la facilidad de implementacion que entrega ´
el primero mencionado. Para lograr que el transistor este en conducci ´ | on (MOSFET-p), es necesario tener ´
una caída de tension´ gate-surtidor (Vgs) que cumpla con los rangos de operacion del transistor, por ello el ´
valor mínimo de tension necesario para la conducci ´ | on debe ser ´ | Vg(min) = Vin − Vgs(th)

1
, Figura 7. En
cambio, el MOSFET-n requiere un circuito de mayor complejidad para ser disparado. A diferencia del canal
p, para que el transistor canal n entre en zona de conduccion se requiere que la tensi ´ | on de ´ | gate sea como

mínimo Vg(min) = Vload+Vgs(th)

2
, Figura 7, aumentando así la dificultad para obtener este valor. El metodo ´ utilizado para lograr esto se lo llama bootstrapping o circuito de bootstrap.

Gate

Vgs(th) = 2 V

Drenador

12 V

Surtidor

Gate

Vgs(th) = −2 V

Surtidor

12 V

Drenador

Carga

Carga

MOSFET-n

MOSFET-p

Para disparar

Vg(min) ≥ 14 V

Para disparar

Vg(min) ≥ 10 V

Figura 7: MOSFET-n vs MOSFET-p.

Existen diversas formas de controlar el voltaje medio de salida del convertidor, entre las dos formas mas´ conocidas se encuentra el PWM (Pulse Width Modulation, modulacion por ancho de pulso) y el PFM, Fi- ´
gura 8. En el primero de los casos lo que se modifica es el tiempo de encendido, manteniendose el per ´ | íodo
constante. A diferencia de PFM donde el período es el que se modifica (cambia la frecuencia de conmu-
tacion), pero el tiempo de encendido se mantiene constante, por ejemplo, en un ´ | 50 % del duty, (ROHM
Semiconductor, 2016). El metodo m ´ | as elegido para los convertidores Buck es el PWM. ´
1Vg, tension de ´ | gate. Vin, tension de entrada. ´
2Vload, tension de carga. ´

Figura 8: Tipos de modulaciones mas usados. ´ Fuente: (Peterson, 2023)

Otro punto importante de los convertidores es el modo de operacion, el mismo puede operar en dos ´ formas, CCM (Continuous Conduction Mode, modo de conduccion continua) y DCM (Discontinuous Con- ´
duction Mode, modo de conduccion discontinua); en el primer caso, la corriente a trav ´ | es del inductor de ´
salida se mantiene siempre positiva, sin alcanzar el valor cero durante el período de conmutacion. En cam- ´ bio, en el modo DCM, la corriente en el inductor llega a ser nula en determinados instantes del período de conmutacion, Figura 9. ´

Cuando el convertidor es controlado de forma digital, estos modos de conduccion suelen presentarse de- ´ pendiendo de la carga utilizada en el convertidor, de modo que a una carga de mayor consumo el convertidor actua en modo CCM y para el caso contrario en DCM. ´

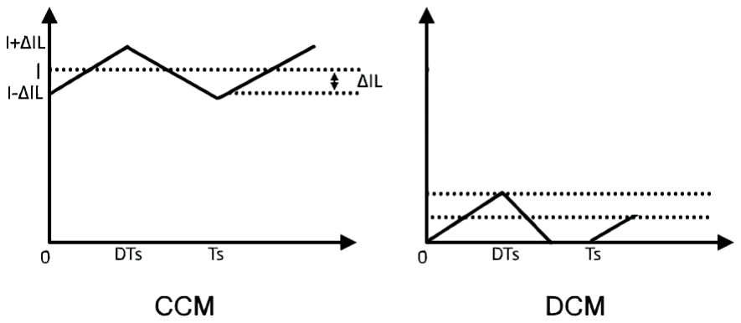
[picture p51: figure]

Figura 9: Modos de funcionamiento. Fuente: (Electrical Technology, 2020)

### 13.2.1. Funcionamiento del convertidor

Modo encendido

IL

## + V dc

Figura 10: Interruptor en conduccion. ´

En un primer momento, cuando el interruptor se encuentra abierto, la corriente en el circuito es nula; luego de cerrado por primera vez, la corriente comienza a incrementarse, por lo que el inductor genera una tension opuesta en respuesta a la corriente de la fuente. En este momento, el diodo se encuentra polarizado ´ de forma inversa, de modo que toda la corriente de entrada se aplica en el inductor, almacenando energía en forma de campo magnetico, Figura 10. ´

El voltaje de caída mencionado contrarresta el voltaje de la fuente, generando una reduccion en el voltaje ´
a traves de la carga. Luego de algunos ciclos de conmutaci ´ | on, la tasa de cambio de la corriente disminuye, ´
y el voltaje a traves del inductor tambi ´ | en lo hace, haciendo que la tensi ´ | on en la carga aumente. ´

Figura 11: Tension y corriente en el inductor. ´ Fuente: (Electrical Technology, 2020)

En la Figura 11 se observa que, mientras el interruptor conduce, la corriente a traves del inductor aumenta ´ llegando a su valor maximo. En el momento en que se apaga el interruptor la corriente comienza a disminuir. ´

Modo apagado

Cuando el dispositivo de conmutacion pasa a su estado de no conducci ´ | on, la fuente es removida del ´
circuito, haciendo que la corriente disminuya. La disminucion de la corriente produce una ca ´ | ída de tension´
en el inductor, inversa a la que había cuando se encontraba en estado de encendido, esto hace que la bobina funcione como una fuente de corriente hacia la carga por medio del campo magnetico almacenado. Esta ´ corriente solo fluye mientras la fuente se mantiene desconectada del circuito, Figura 12.

IL

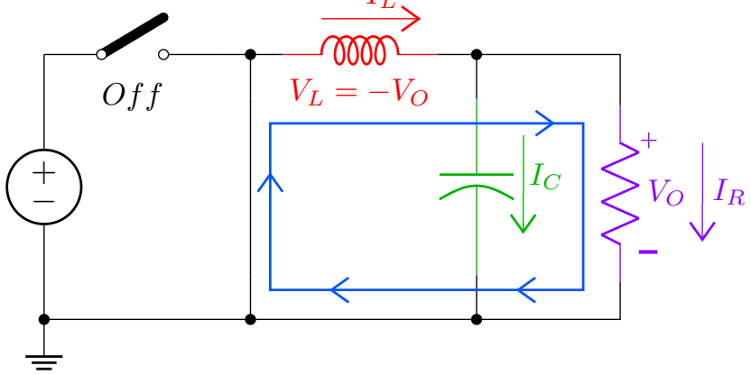
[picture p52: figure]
Off

## + V dc

Figura 12: Interruptor en estado de no conduccion. ´

El interruptor se encuentra abierto, y el inductor cambia su polaridad para oponerse a la descarga que esta sufriendo el mismo, quedando el diodo polarizado en forma directa. ´

Una vez que el convertidor se encuentra en un modo normal de funcionamiento, la corriente por la carga queda determinada por la suma de la corriente aportada por la fuente de alimentacion, y por la corriente ´ producto del campo magnetico almacenado en el inductor. En este caso, siempre se tiene una corriente ´ mayor en la carga. Ese aumento de corriente, debido a la corriente de fuente y a la corriente del inductor, da lugar a que el voltaje se vea disminuido en la carga para preservar la potencia del convertidor.

13.3. Calculos para el dise ´ | nõ
El modulo convertidor reductor se dise ´ | na para una tensi ˜ | on de entrada de ´ | 12 V y una corriente de entrada
de 3 A. Para facilitar la visualizacion de las distintas se ´ | nales, tanto de corriente como de tensi ˜ | on necesarias ´
para la interpretacion del circuito, la tensi ´ | on de salida se establece con un rango completo de ´ | | 0 V a 12 V, al
igual que la corriente. Esto permite que aumenten las posibilidades de pruebas en el laboratorio, y genera
una mayor versatilidad para observar el funcionamiento del modulo en cuesti ´ | on. ´
Los calculos de dise ´ | no se basan en un informe de aplicaci ˜ | on de ´ | Texas Instruments (Hauke, 2011).

Criterios de disenõ

El modulo se calcula para una corriente de ´ | 2,4 A la cual representa un 80 % de la corriente entregada por
la fuente, esto es con el objetivo de mantener un margen de seguridad evitando exigir los componentes.

Potencia del convertidor 36W.

R =

12 V
2,4 A = 5 Ω.

Ripple

- ∆Vout = 2 % Vout = 0,02 · 12 V = 0,24 V
- ∆IL = 30 % Iout = 0,3 · 2,4 A = 0,72 A
Frecuencia de conmutacion ( ´ | fs), 19 kHz.
Rendimiento teorico considerado, ´ | η = 90 %.

Se elige como transistor de conmutacion de potencia el IRF9540, (International Rectifier, 2004), la se- ´
leccion del mismo se basa en la disponibilidad y en su amplio campo de aplicaci ´ | on, lo que permite que en ´
caso de falla o rotura del modulo sea f ´ | acil de reemplazar. ´

### 13.3.1. Ciclo de trabajo maximo ´

Dmax =

Vout

Vin η

=

6 V
12 V 0,9
= 0,55 | (2)
Dentro del calculo es considerado el rendimiento porque el convertidor tambi ´ | en entrega energ ´ | ía. Este
calculo proporciona un valor m ´ | as realista del ciclo de trabajo m ´ | aximo en comparaci ´ | on con la ecuaci ´ | on que ´
no incluye el factor de rendimiento.

### 13.3.2. Capacitor de salida mínimo

Coutmin =

∆IL

8 fs ∆Vout

=

0,72 A
8 · 19 × 10³ Hz 0,24 V
= 19,74 µF | (3)

Cualquier capacidad mayor a la calculada puede ser utilizada sin afectar el correcto funcionamiento del
convertidor. Este tipo de calculos se pueden realizar para convertidores con compensaci ´ | on externa. Para el ´
caso de los internamente compensados, como puede ser un circuito integrado Buck, es recomendable utilizar los valores establecidos en la hoja de datos. El capacitor elegido para el circuito es de 42 µF.

### 13.3.3. Inductor mínimo

Lmin =

(Vin − Vout) Dmax
fs ∆IL

=

(12 V − 6 V) 0,55
19 × 10³ Hz 0,72 A = 241,23 µH | (4)

El valor calculado se considera como mínimo, ya que emplear una inductancia mayor reduce el ripple de

corriente e incrementa la corriente de salida. Sin embargo, tambien implica un aumento en el tama ´ | no f ˜ | ísico
del inductor. Por el contrario, disminuir la inductancia incrementa el ripple y reduce la corriente de salida, aunque permite utilizar un inductor de menor tamano. Por lo tanto, es necesario encontrar un equilibrio ˜
adecuado entre el tamano del inductor y el nivel de ˜ | ripple permitido en la salida. Por ello, el inductor
elegido para el circuito es de 330 µH.

### 13.3.4. Corriente media en diodo

ID = Iout (1 − D) = 2,4 A (1 − 0,55) = 1,08 A | (5)

Este valor determina la corriente media aplicada en el diodo de rectificacion, es recomendable utilizar un ´
Schottky ya que su rapida recuperaci ´ | on lo hace adecuado a las altas frecuencias de trabajo del convertidor. ´
Ademas, la tensi ´ | on soportada por el diodo debe ser al menos un ´ | 30 % mas que la tensi ´ | on de salida del ´
convertidor.

El diodo elegido para cumplir estas características es el SR560, (HY Electronic, 2020).

### 13.3.5. Red Snubber

El calculo de la red Snubber se basa en una nota de aplicaci ´ | on de Toshiba (Toshiba, 2018), tomando ´
como referencia algunos de sus criterios, ademas de criterios propios. ´
Se supone un valor de inductancia parasita t ´ | ípico de 50 nH y que la capacitancia parasita es ´ | CP = COSS,
siendo COSS la capacitancia de salida del transistor.

fring, representa la frecuencia de las oscilaciones existentes en la conmutacion del transistor, no se tiene ´
este valor, pero se calcula en funcion de un valor estimado de inductancia par ´ | asita, con el fin de probar el ´
circuito con red de snubber y sin la misma.

Red de Snubber para transistor IRF9540

COSS = 400 pF ≈ Csnub(min)

fring =

1
2π ∗

√
LP ∗ CP
= 35,6 MHz | (6)

Rsnub =

1

2πfringCsnub

= 11,2 Ω | (7)

Red de Snubber para transistor 2N2222

Cobo = 8 pF ≈ Csnub(min). Cobo, capacitancia de salida de transistores BJT.

fring =

1
2π ∗

√
LP ∗ CP
= 251,65 MHz | (8)

Rsnub =

1

2πfringCsnub

= 79 Ω | (9)
Los calculos que se presentan a continuaci ´ | on, siguen la t ´ | ecnica descrita en un art ´ | ículo tecnico de ´ | Texas
Instruments, (Betten, 2016). Este metodo consiste en probar el circuito en dos condiciones, la primera es ´
sin ninguna red de Snubber para poder determinar la frecuencia de oscilacion real; la segunda condici ´ | on´
es conectando un capacitor en paralelo al transistor y medir la frecuencia nuevamente. El objetivo de esta prueba es que al conectar el capacitor, la frecuencia medida sea de al menos un 50 % menor a la frecuencia real de oscilacion del circuito. ´

La tension medida es entre colector y emisor de un transistor BJT, o entre drenador y surtidor de un ´ transistor MOSFET. Estas oscilaciones que se presentan en las Figuras 13 y 14, son las que aparecen en el momento en el que los transistores cambian su estado, de encendido a apagado o viceversa. Esta frecuencia es la denominada anteriormente como frecuencia de ring, la cual no es deseada, teniendo que disminuir al maximo su efecto. ´

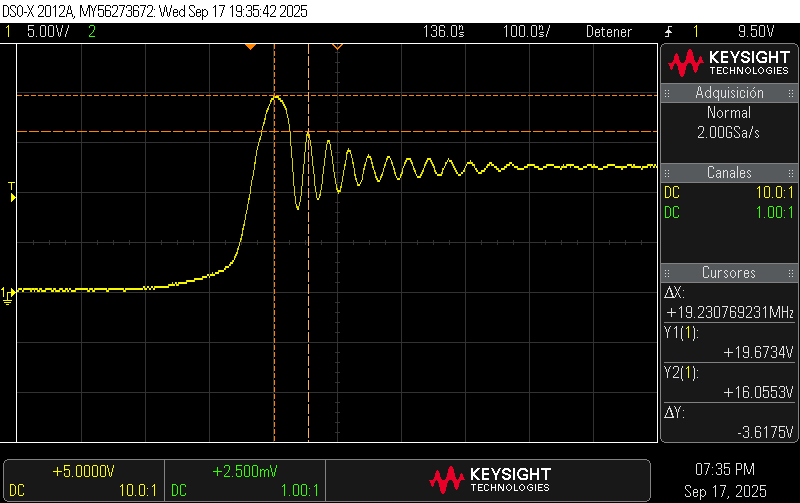
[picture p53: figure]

(a) Sin capacitor. | (b) Con capacitor de 400 pF.

Figura 13: Resultados en transistor IRF9540 en circuito real

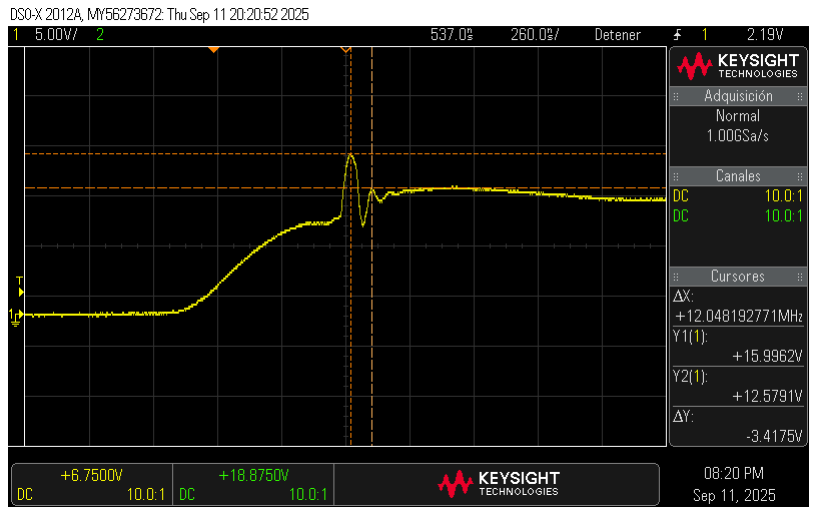
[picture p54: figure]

(a) Sin capacitor. | (b) Con capacitor de 2 pF³

Figura 14: Resultados en transistor 2N2222 en circuito real

En las Figuras 13 y 14 se puede observar el corrimiento de frecuencia necesario para los siguientes calculos. ´

Nuevos valores para red de Snubber de transistor IRF9540

Datos para la obtencion de nuevos valores de red de Snubber: ´

Frecuencia de oscilacion sin capacitor, ´ | f0 = 19,23 MHz, Figura 13a.
Frecuencia de oscilacion con capacitor, ´ | f1 = 11,9 MHz, Figura 13b.

Capacitor paralelo, C1 = 400 pF.

m =

f0
f1

= 1,62

Se calcula la capacitancia e inductancia parasita. ´

C0 =

C1
m² − 1

= 246,24 pF

L =

m² − 1
(2π f0)

2 C1

= 278,17 nH

Se determinan los nuevos valores de red de Snubber en funcion del corrimiento de frecuencia. ´

Csnub = 3 C0 = 738,72 pF | (10)

Rsnub =

r
L
C0
= 33,61 Ω | (11)

3
Se utiliza un capacitor de 2 pF en lugar del utilizado para el calculo en la Ecuaci ´ | on (8), ya que el corrimiento necesario de ´
frecuencia fue mas coherente con el mismo. ´

Se utiliza un valor de 1 nF para el capacitor y de 33 Ω para la resistencia de la red.

Nuevos valores para red de Snubber de transistor 2N2222

Datos para la obtencion de nuevos valores de red de Snubber: ´

Frecuencia de oscilacion sin capacitor, ´ | f0 = 19,23 MHz, Figura 14a.
Frecuencia de oscilacion con capacitor, ´ | f1 = 12,05 MHz, Figura 14b.

Capacitor paralelo, C1 = 2 pF.

m =

f0
f1

= 1,6

Se calcula la capacitancia e inductancia parasita. ´

C0 =

C1
m² − 1

= 1,28 pF

L =

m² − 1
(2π f0)

2 C1

= 53,43 nH

Se determinan los nuevos valores de red de Snubber en funcion del corrimiento de frecuencia. ´

Csnub = 3 C0 = 3,84 pF | (12)

Rsnub =

r
L
C0
= 6460,82 Ω | (13)

Se utiliza un valor de 5 pF para el capacitor y de 6,8 kΩ para la resistencia de la red.

En las Figuras 15 y 16 se encuentran los resultados con los nuevos valores de red de Snubber, donde se
puede determinar una amplia disminucion de la frecuencia de oscilaci ´ | on no deseada en la conmutaci ´ | on de ´
los transistores.

(a) Unicamente con capacitor en paralelo, Figura 13b. ´ | (b) Con nuevos valores de red de Snubber.

Figura 15: Resultados en transistor IRF9540 en circuito real

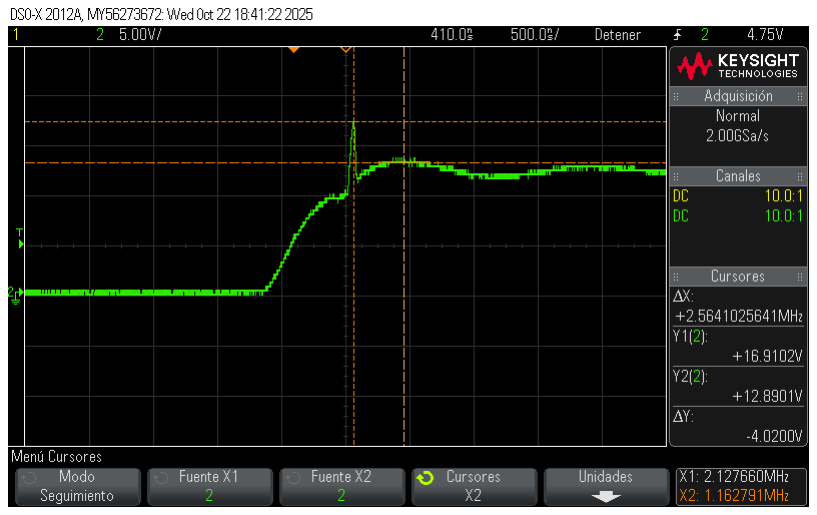
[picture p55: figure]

(a) Unicamente con capacitor en paralelo, Figura 14b. ´ | (b) Con nuevos valores de red de Snubber.

Figura 16: Resultados en transistor 2N2222 en circuito real

### 13.3.6. Realimentacion microcontrolador ´

Para poder realizar un control digital es necesario tener una variable manipulada y una controlada. La primera, para el caso del convertidor Buck, es el PWM que se aplica al terminal gate del transistor MOSFET-p; la segunda se corresponde a la tension de salida realimentada al microcontrolador. ´

Para lograr realimentar la tension de salida se utiliza un divisor de tensi ´ | on, encargado de adecuar la ´
tension de salida con rango ´ | 0 V a 12 V, a tensiones manejables por el microcontrolador, rango 0 V a 3,3 V.
En la Ecuacion (14) se presenta el c ´ | alculo de las resistencias del divisor de tensi ´ | on, donde ´ | R1 es la resistencia
que se conecta entre la salida y el punto medio del divisor, y R2 es la resistencia que se conecta entre el punto medio y tierra; se presenta graficamente en la Figura 17. ´

Vout =

Vin R2
R1 + R2

(14)

3,3 V = 12 V 4,7 kΩ
R1 + 4,7 kΩ

R1 =12,39 kΩ

R1

R2

GND

Microcontrolador

12 V

Figura 17: Divisor de tension gen ´ erico. ´

### 13.3.7. Filtro RC para ADC

Criterios de diseno - filtro pasa-bajos ˜

fc = 100 Hz

C = 10 µF

fc =

1
2π R C

R =

1
2π fc C
= 159,15 Ω ≈ 150 Ω | (15)

En la Figura 18 se presenta el filtro pasa-bajos utilizado en la entrada del ADC del microcontrolador, este filtro tambien es conocido como RC. ´

R

Entrada | C | Salida

Figura 18: Filtro pasa-bajos generico. ´

Tanto el filtro como el divisor de tension anteriormente mencionados, Figuras 17 y 18; y calculados, ´ Ecuaciones (14) y (15), son importantes para poder realizar correctamente un control digital.

El objetivo de esta medicion es poder realizar un control preciso de la tensi ´ | on entregada a la carga, ´
por ello se aplica un lazo cerrado donde la tension de salida se la compara con una tensi ´ | on de referencia ´
(setpoint), para así aplicar la correccion del ciclo de trabajo del PWM y lograr la conmutaci ´ | on correcta del ´

transistor. Si la carga demanda menos corriente, la tension tiende a subir y viceversa, por ello la utilidad ´ de un control para ajustar el ciclo de trabajo en funcion de la carga conectada al convertidor. Hay diversas ´
tecnicas de control, dentro de las m ´ | as utilizadas, PID. ´

### 13.3.8. Transistor BJT como driver de MOSFET

Como el microcontrolador elegido es el ESP32-S3, el mismo presenta en la hoja de datos que la corriente acumulada de todos los pines es de 1,5 A, por ende, si el microcontrolador posee 45 pines físicos, cada uno cuenta de 33,33 mA de corriente. El transistor elegido para este uso es el 2N2222, posee una corriente de
colector maxima de ´ | 600 mA y un β de 100 para una corriente de colector de 150 mA.

Rb(min) =

V
Ib

=

3,3 V

150 mΩ
100
= 2,2 kΩ | (16)

Se elige una resistencia de 2,2 kΩ, Figura 19. La principal funcion de utilizar esta resistencia es limitar la ´ corriente que se demanda al microcontrolador, pero a su vez es necesaria para que tanto el microcontrolador
como el transistor no se danen debido a corrientes indeseadas o par ˜ | asitas mayores a la corriente deseada para ´
el correcto funcionamiento. Una consideracion por tener es que, cuanto mayor es el valor de resistencia, el ´ tiempo de respuesta del transistor disminuye.

Figura 19: Transistor 2N2222 como driver de MOSFET-p.

### 13.3.9. Mediciones de corriente

Medicion de corriente en inductor - Unidireccional ´

Para facilitar la medicion de corriente y poder visualizar el comportamiento de la misma en operaci ´ | on´
normal del convertidor, se utiliza un amplificador de corriente INA199B2, el cual es un amplificador operacional utilizado en su configuracion diferencial, Figura 20 (Texas Instruments, 2023). ´

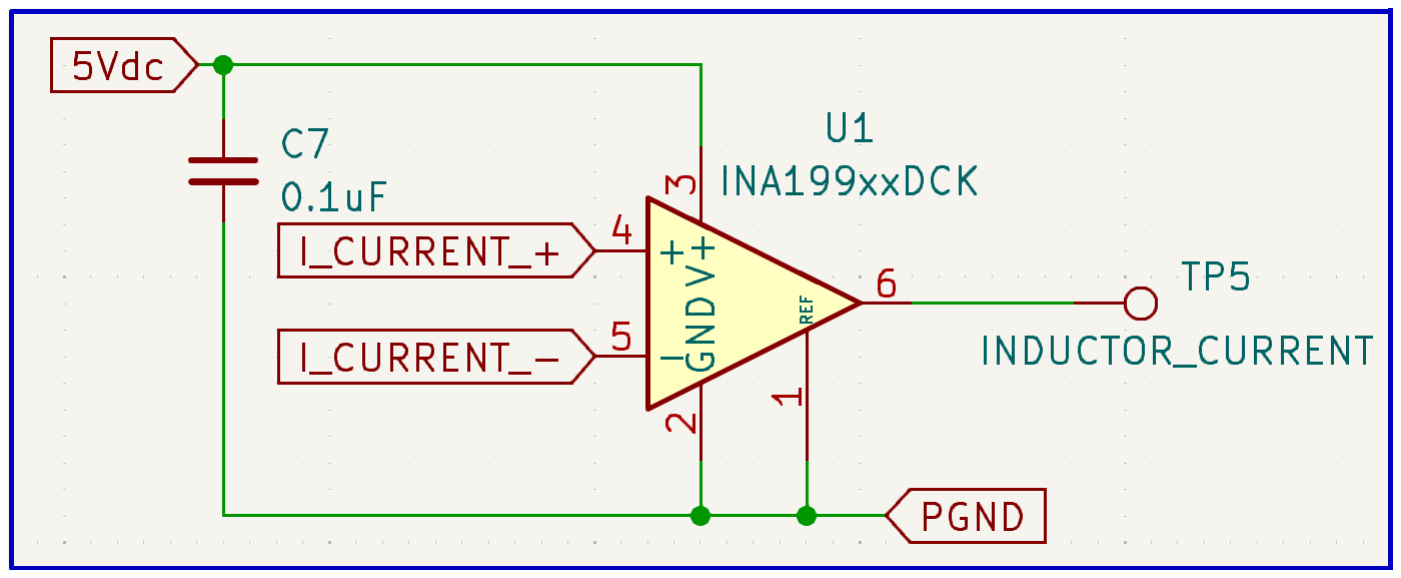
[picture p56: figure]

Figura 20: Medicion de corriente unidireccional con INA199B2. ´

Informacion´ util para c ´ | alculos ´

Ganancia = 100 V/V.

VCC = 5 V.

Vout = 0,05 V a 4,8 V.

Informacion obtenida de la hoja de datos del amplificador INA199B2, (Texas Instruments, 2023). ´

Criterio de disenõ

VRshunt = 20 mV a 50 mV.

Rshunt = 6,8 mΩ a 15 mΩ.

PRshunt = 61,2 mW a 135 mW.

Estos valores fueron calculados para una corriente de 3 A, que es la corriente maxima determinada para ´ el diseno del convertidor. ˜

En una primera instancia se calcula el valor maximo de tensi ´ | on en la resistencia ´ | shunt, VRshunt , tenien-
do en cuenta la tension de salida m ´ | axima del integrado, ´ | Vout = 4,8 V; y la ganancia del amplificador,
Ganancia = 100; Ecuacion (17). ´
Vout =Ganancia VRshunt | (17)

4,8 V =100 VRshunt

VRshunt =

4,8 V
100

= 48 mV

Luego se determina el valor de la resistencia shunt, Rshunt, a partir de la tension m ´ | axima en la resistencia ´
shunt y la corriente maxima del convertidor, Ecuaci ´ | on (18). ´

Rshunt =

VRshunt

Iout(max)

=

48 × 10⁻³ V
3 A | = 0,016 Ω | (18)
Se elige una resistencia shunt de 10 mΩ por la disipacion de potencia. Adem ´ | as, entrega un buen rango ´
de tension a la salida del amplificador, ´ | Vout = 0,05 V a 3 V.

Medicion de corriente en capacitor - Bidireccional ´

Como la corriente en el capacitor es bidireccional, se debe realizar un arreglo de resistencias al amplificador de corriente para poder medir este tipo de corriente, Figura 21.

Es comun en esta configuraci ´ | on de amplificador diferencial la necesidad de utilizar una tensi ´ | on de re- ´
ferencia del 50 % de la tension de alimentaci ´ | on del integrado, con el fin de lograr que la corriente en la ´
resistencia shunt pueda ser medida en ambos sentidos. Cuando Vshunt < Vref la corriente circula en un sentido, y cuando Vshunt > Vref la corriente circula en sentido contrario al anterior.
Para lograr la tension de referencia se usa un divisor de tensi ´ | on para obtener el voltaje requerido, ´ | 2,5 V;
a su vez se aplica un operacional como seguidor de tension por recomendaci ´ | on propia del fabricante. ´

Figura 21: Medicion de corriente bidireccional con INA199B2. ´

Criterio de disenõ

Vref =

5 V 10 kΩ
10 kΩ+10 kΩ = 2,5 V.
Vout =Vref + Ganancia VRshunt | (19)

4,8 V =2,5 V + 100 VRshunt

VRshunt =

4,8 V − 2,5 V
100

= 0,023 V

Rshunt =

VRshunt

Iload

=

23 mV
3 A = 7,67 mΩ | (20)

El procedimiento presentado en las Ecuaciones (19) y (20) es similar al realizado para la medicion de ´
corriente unidireccional, con la unica diferencia del voltaje de referencia, ´ | | Vref , fijado por el divisor de
tension. ´

Se opta por utilizar una resistencia shunt de 5 mΩ, ya que si se eligiese una resistencia mayor, la tension´
entregada por el amplificador estaría muy proxima al valor m ´ | aximo manejable por el mismo; adem ´ | as es un ´
valor comercial comun y estandarizado, f ´ | acil de conseguir. ´

13.3.10. Seleccion de carga con Rel ´ | é

Para experimentar el comportamiento del convertidor Buck frente a diferentes cargas, se utiliza un relé controlado por un microcontrolador permitiendo elegir entre dos cargas: una resistiva y otra inductiva, con el fin de notar las diferencias que puede causar un simple cambio de carga en la operacion normal del ´ convertidor.

Para conmutar entre los dos estados del rele, normal abierto o normal cerrado, se utiliza un transistor ´ BJT como driver, Figura 22.

Figura 22: Circuito driver para rele.´

13.3.11. Calculo de disipador para MOSFET de conmutaci ´ | on´

Una vez seleccionado el transistor MOSFET-p es necesario determinar la disipacion de potencia que ´ experimenta en la operacion normal del convertidor. Para ello, se divide la potencia total en resistiva y de ´ conmutacion. Como lo indica el nombre, la primera se debe a la resistencia drenador-surtidor de transistor; ´
y la segunda es debido a la conmutacion del mismo en la operaci ´ | on del convertidor Buck, (Analog Devices, ´
2002).
Ptotal = Presistive + Pswitching | (21)

Para determinar si es necesario el uso de un disipador en el transistor, el primer paso es asumir una temperatura de juntura maxima, respetando el rango determinado por la hoja de datos. Para el caso del ´ IRF9540 se asume una temperatura de juntura de TJ(hot) = 120 ◦C
4

Una vez determinado este valor se procede a calcular el valor de RDS(on) con el valor elegido de temperatura de juntura.

RDS(on)hot =RDS(on)spec -
1 + 0,005 (TJ(hot) − Tspec)
(22)
=0,117 Ω [1 + 0,005 (120 ◦C − 25 ◦C)]

=0,172 Ω

4
Para este calculo, se mantienen los valores de temperatura en grados Celsius, ya que solo intervienen en diferencias matem ´ | ati- ´
cas.

Luego, se calcula la potencia disipada debido a la resistencia anteriormente calculada.

Presistive =

I

2

load RDS(on)hot Vout

Vin

(23)

=

(3 A)²
0,172 Ω
1

=1,55W

A su vez, se determina cuanta potencia se disipa debido a la conmutaci ´ | on del transistor. ´

Pswitching =

Crss V

2
in fsw Iload

Igate

(24)

=

240 pF (12 V)² 19 kHz 3 A
100 mA
=0,02W

Partiendo de la Ecuacion (21) se obtiene la potencia que debe disipar el transistor MOSFET-p. Los ´
valores estan calculados para una potencia de salida de ´ | 36W.

Ptotal = 1,55W + 0,02W = 1,57W

Resistencia termica ´

Partiendo de la potencia total, es requisito determinar cuanto es el aumento de la temperatura de juntura ´ debido a la potencia disipada.

TJ(rise) =Ptotal ΘJA | (25)

=1,57W 62 ◦C/W

=97,22 ◦C

Luego se debe determinar el valor de la temperatura ambiente teorica que debe existir para lograr la ´ temperatura de juntura anteriormente calculada.

Tambiente =TJ(hot) − TJ(rise)
(26)
=120 ◦C − 97,22 ◦C

=22,78 ◦C

Si la temperatura ambiente real excede la temperatura ambiente calculada, Tambiente = 22,78 ◦C, es
necesario emplear un disipador termico. Debido a que esta temperatura es ligeramente menor a ´ | 25 ◦C, se
emplea un pequeno disipador de ˜ | 17 × 11 × 5 mm.

### 13.3.12. Eficiencia del convertidor

La eficiencia es un termino ´ | util para determinar cu ´ | anto de la potencia que se entrega al convertidor ´
es traspasada a la salida del mismo, se expresa en un porcentaje. Alternativamente, se puede expresar la

eficiencia en termino de las p ´ | erdidas, Ecuaci ´ | on (27); (Raj, 2010). ´

η =

PO
PO + PD

(27)

Las perdidas por disipaci ´ | on incluyen tanto las de conmutaci ´ | on y conducci ´ | on del transistor, como as ´ | í
tambien las que respectan al n ´ | ucleo magn ´ | etico del inductor. Las p ´ | erdidas par ´ | asitas en capacitores, o pistas ´
del circuito no se las considera para el calculo ya que son valores despreciables, en comparaci ´ | on a las otras ´
perdidas mencionadas. ´

PL = I

2

O RDCR = (3 A)²
150 mΩ = 1,35W | | | | (28)
Una vez calculada la disipacion debido al n ´ | ucleo magn ´ | etico del inductor, Ecuaci ´ | on (28) y la disipaci ´ | on´
total producto del transistor de conmutacion, Ecuaci ´ | on (21); se puede calcular la potencia disipativa o de ´
perdidas te ´ | orica que tiene el circuito, Ecuaci ´ | on (29). ´
PD = PL + Ptotal = 1,35W + 1,55W = 2,9W | (29)
El rendimiento teorico del convertidor est ´ | a dado por, Ecuaci ´ | on (30). ´

η =

PO
PO + PD

(30)

=

36W
36W + 2,9W
= 0,925 ≈ 92,5 % | (31)

### 13.4. Simulacion´

Para corroborar el correcto funcionamiento del circuito previo a su elaboracion f ´ ísica, se realiza la simulacion del mismo utilizando el software gratuito LTspice, (Analog Devices, 2025). ´

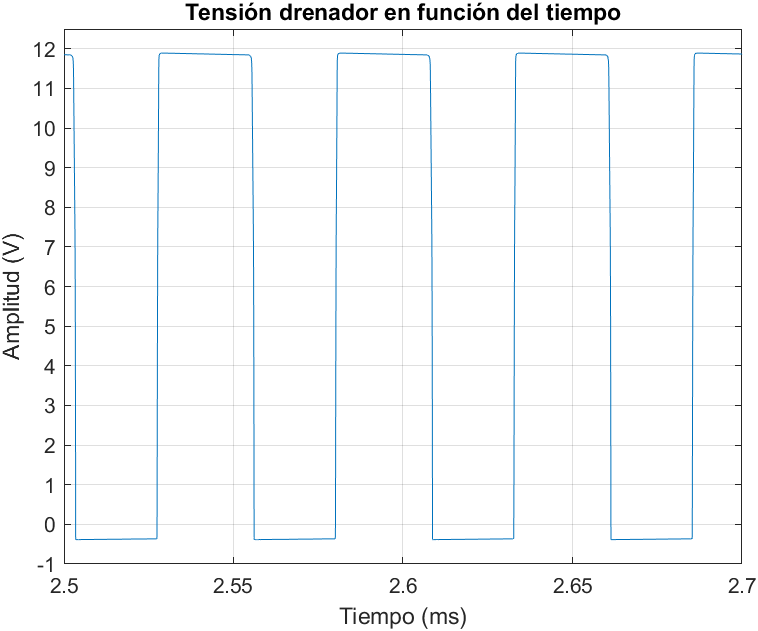
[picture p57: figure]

(a) Tension en drenador de transistor de conmutaci ´ | on. ´ | (b) Tension de salida en simulaci ´ | on. ´

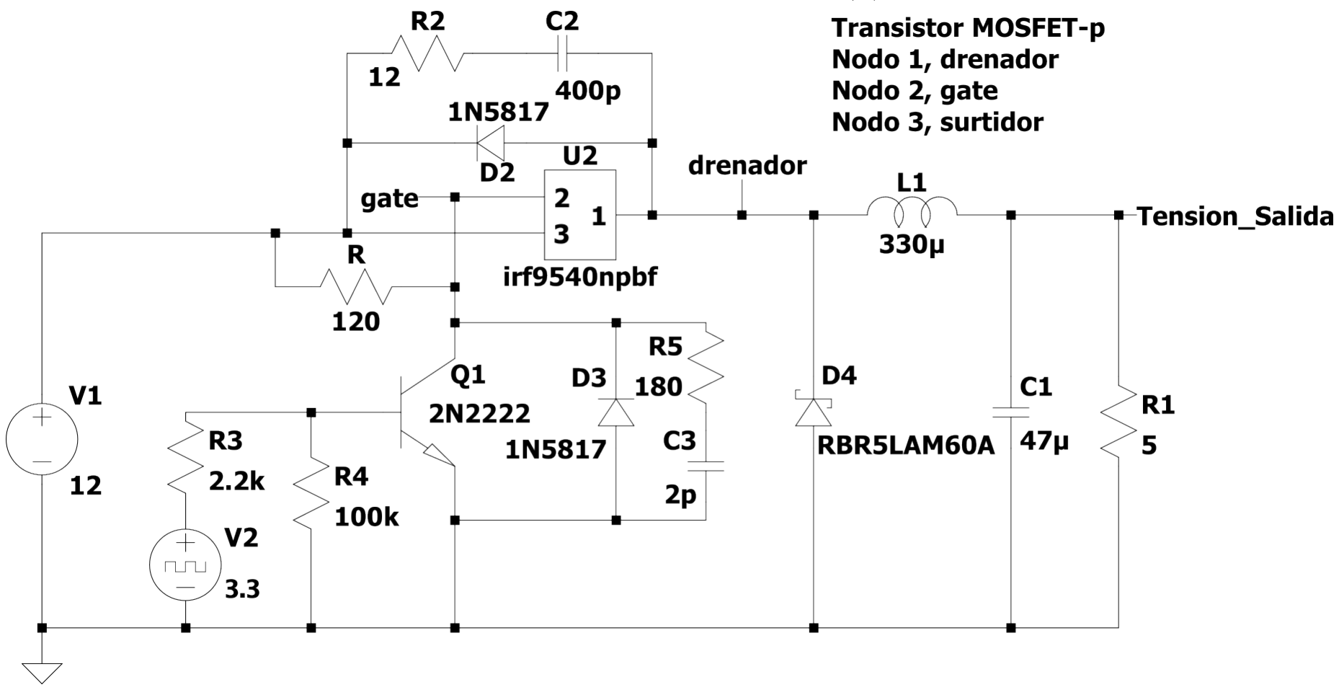
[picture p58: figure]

(c) Circuito utilizado para simular⁵ .
Figura 23: Resultados de la simulacion con un ciclo de trabajo del ´ | 50 %.

Como se observa en la Figura 23 el circuito funciona segun lo esperado, donde al aplicar un ciclo de ´
trabajo del 50 % aproximadamente, la tension de salida es de ´ | 6 V. Cabe aclarar que las Figuras 23a y 23b
estan tomadas en r ´ | egimen permanente, sin considerar los posibles efectos transitorios del circuito. ´

## 14. Modulo recortador de onda ´

Uno de los metodos m ´ | as simples para controlar la potencia entregada a una carga de corriente alterna es ´
mediante el uso de un recortador. Este metodo se basa en la utilizaci ´ | on de un tiristor para recortar la onda ´
de tension aplicada a la carga, permitiendo as ´ | í regular la potencia entregada. Al recortar la onda, se reduce
la tension RMS aplicada a la carga, lo que a su vez produce una reducci ´ | on de potencia entregada. ´
Este metodo tiene varias desventajas, como una baja eficiencia y alta distorsi ´ | on arm ´ | onica. Sin embargo, ´
su simplicidad y bajo costo es la razon por la cual se sigue utilizando en aplicaciones espec ´ | | íficas donde se
requiere un control de potencia simple y economico. ´
Se elige este modulo para el proyecto ya que es un buen primer paso en la electr ´ | onica de potencia, donde ´
se puede realizar un enfoque centralizado en el funcionamiento y control de un semiconductor como el

5
Se utilizo el diodo RBR5LAM60A por disponibilidad del modelo para simulaci ´ | on. Las caracter ´ | ísticas se corresponden con
las de SR560.

TRIAC (Triode for Alternating Current, Triodo para Corriente Alterna en espanol). ˜

14.1. Interaccion del usuario: control y verificaci ´ | on experimental ´
El modulo recortador de onda est ´ | a dise ´ | nado para que el usuario pueda seleccionar entre dos modos de ˜
control: analogico y digital. En el modo de control anal ´ | ogico, el usuario utiliza un potenci ´ | ometro dentro del ´
gabinete para modificar una resistencia, lo que cambia el tiempo de carga de un capacitor y el tiempo de
disparo del TRIAC, variando la potencia entregada a la carga (dos lamparas de ´ | 24 V en serie). En el modo
de control digital, el usuario puede directamente elegir el tiempo de disparo del TRIAC, en base al cruce por cero de la tension de corriente alterna de entrada. Mediante distintos puntos de prueba, el usuario puede con ´
un osciloscopio visualizar diferentes ondas, como la tension aplicada a la carga, tensi ´ | on en TRIAC, carga y ´
descarga de capacitor, entre otras. De esta manera, el usuario aprende sobre el funcionamiento del circuito y verificar experimentalmente los conceptos teoricos. ´

### 14.2. Base teorica ´

### 14.2.1. Tiristores y el TRIAC

Los tiristores pueden adoptar diversas formas, pero comparten ciertas características. Todos son interrup-
tores de estado solido que act ´ | uan como circuitos abiertos capaces de soportar la tensi ´ | on nominal hasta su ´
activacion. Al activarse, los tiristores se convierten en circuitos de corriente de baja impedancia y perma- ´
necen en esa condicion hasta que la corriente se detiene o cae por debajo de un valor m ´ | ínimo denominado
nivel de retencion. Una vez activado un tiristor, la corriente de activaci ´ | on puede eliminarse sin apagar el ´
dispositivo, (ON Semiconductor, 2005)

El TRIAC es un tiristor bidireccional ampliamente utilizado en la electronica de potencia, en especial en ´ aplicaciones menores a 40 A. Puede ser pensado como dos SCR (Silicon Controlled Rectifier, Rectificador
controlado de silicio en espanol) en antiparalelo con su terminal de compuerta unidos. Adem ˜ | as, puede ser ´
disparado por una senal de corriente alterna o una de corriente continua positiva o negativa. ˜

### 14.2.2. Características del TRIAC

(a) Símbolo del TRIAC
(b) Curva corriente-voltaje de un TRIAC

Figura 24: Características del TRIAC. Fuente: (Rashid, 2015)

Como un TRIAC es un dispositivo bidireccional, sus terminales no se pueden designar como anodo ´ y catodo. Si la terminal MT2 es positiva con respecto a la terminal MT1, el TRIAC se puede encender ´ aplicando una senal de compuerta positiva entre la compuerta G y la terminal MT1. Si la terminal MT2 ˜ es negativa con respecto a la terminal MT1, se enciende aplicando una senal de compuerta negativa entre ˜ la compuerta G y la terminal MT1. No es necesario tener ambas polaridades de senales de compuerta, y ˜
un TRIAC se puede encender con una senal de compuerta ya sea positiva o negativa. En la pr ˜ | actica, las ´
sensibilidades varían de uno a otro cuadrante y por lo comun los TRIAC funcionan en el cuadrante I (voltaje ´ y corriente de compuerta positivos), o en el cuadrante III (voltaje y corriente de compuerta negativos), (Rashid, 2015)

En la electronica de potencia, el TRIAC puede ser utilizado en diversas aplicaciones: Interruptor de CA, ´
conmutador de punto cero, control de fase, entre otras. La aplicacion del TRIAC utilizada en este m ´ | odulo ´
es la de control de fase, para subsecuentemente regular la potencia entregada a la carga.

### 14.2.3. Control de fase con tiristores

El control de fase es un metodo que utiliza el TRIAC para aplicar la alimentaci ´ | on de CA a la carga ´
durante una fraccion controlada de cada ciclo. En este modo de funcionamiento, el TRIAC se mantiene ´ en estado de apagado o abierto durante una parte de cada ciclo positivo y negativo, y luego se activa en un momento del semiciclo determinado por el circuito de control. En estado de encendido, la corriente del
circuito esta limitada ´ | unicamente por la carga; es decir, toda la tensi ´ | on de l ´ | ínea (menos la caída de tension´
directa del TRIAC) se aplica a la carga, (ON Semiconductor, 2005).
El metodo m ´ | as com ´ | un de control electr ´ | onico de potencia de CA se denomina control de fase. La Figura ´
25 ilustra este concepto. Durante la primera parte de cada semiciclo de la onda sinusoidal de CA, se abre un
interruptor electronico para impedir el flujo de corriente. En un ´ | angulo de fase espec ´ | ífico α, este interruptor
se cierra para permitir que se aplique toda la tension de l ´ | ínea a la carga durante el resto de ese semiciclo. La
variacion de ´ | α controla la parte de la onda sinusoidal total que se aplica a la carga (area sombreada) y, por ´
lo tanto, regula el flujo de potencia hacia la carga, (ON Semiconductor, 2005).

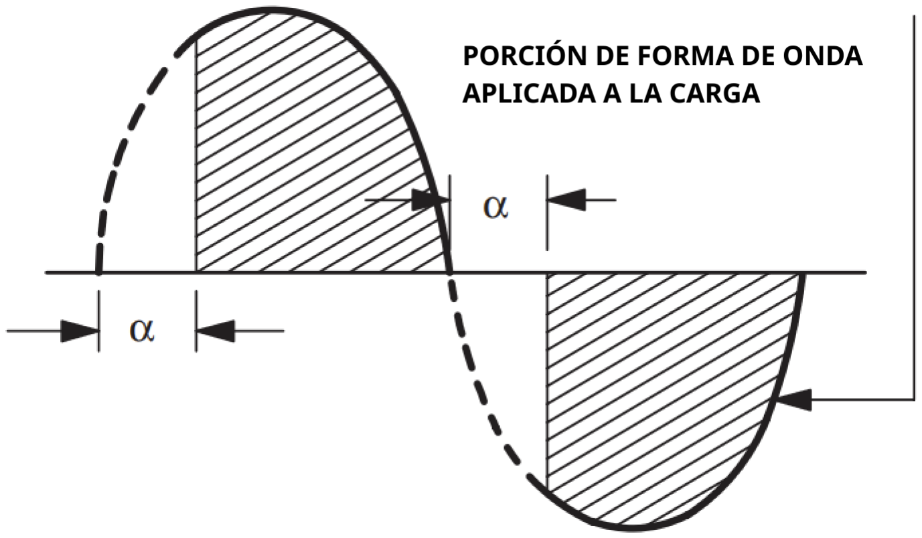
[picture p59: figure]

Figura 25: Control de fase de onda de corriente alterna. Fuente: (ON Semiconductor, 2005)

El circuito mas simple para lograr el control de fase se muestra en la Figura 26. En este caso, el interruptor ´
electronico es un TRIAC (Q) que se activa mediante un peque ´ | no pulso de corriente en su compuerta. El ˜
TRIAC se desactiva automaticamente cuando la corriente que lo atraviesa pasa por cero. En el circuito ´ mostrado, el capacitor CT se carga durante cada semiciclo mediante la corriente que fluye a traves de la ´
resistencia RT y la carga. El hecho de que la carga este en serie con ´ | RT durante esta parte del ciclo tiene
poca importancia, ya que la resistencia de RT es mucho mayor que la de la carga. Cuando la tension en el ´
CT alcanza la tension de ruptura del disparador bilateral DIAC (D), se libera la energ ´ | ía almacenada en el
capacitor CT . Esta energía produce un pulso de corriente en el DIAC, que fluye a traves de la compuerta del ´ TRIAC y lo activa. Dado que tanto el DIAC como el TRIAC son dispositivos bidireccionales, los valores de RT y CT determinan el angulo de fase en el que se activa el TRIAC en los semiciclos positivo y negativo de ´ la onda sinusoidal de CA, (ON Semiconductor, 2005).

Figura 26: Circuito basico de control de fase. ´

La forma de onda del voltaje a traves del capacitor para dos condiciones de control t ´ | ípicas (α = 90° y α =
150°) se muestra en la Figura 27. Si se utiliza un SCR en este circuito en lugar del TRIAC, solo se controla un semiciclo de la forma de onda. El otro semiciclo se bloquea, lo que genera una salida de DC pulsante cuyo valor promedio puede variarse ajustando el RT , (ON Semiconductor, 2005).

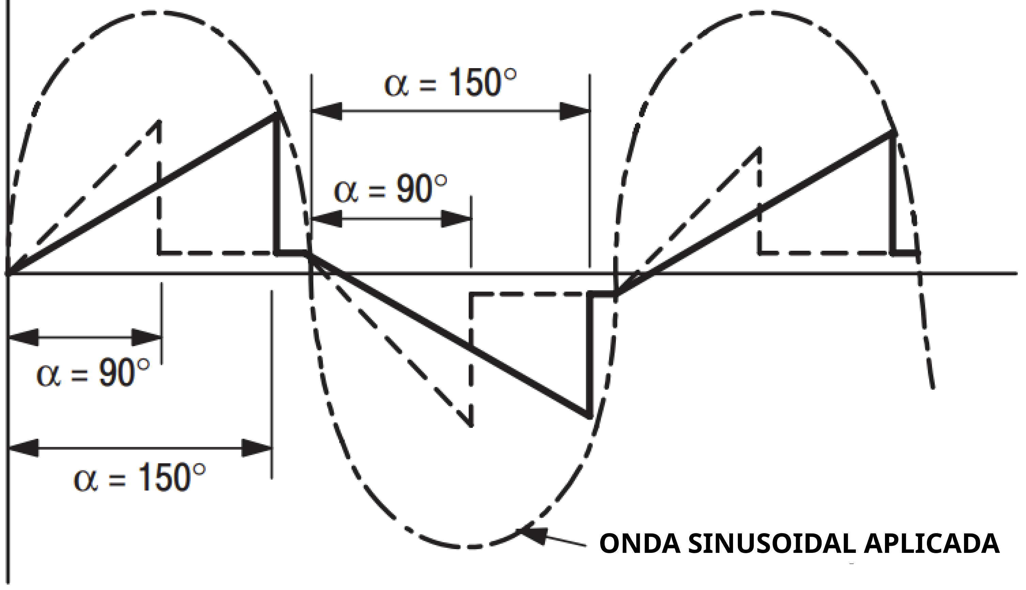
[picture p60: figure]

Figura 27: Tension de capacitor con dos diferentes ´ | angulos de fase. ´
Fuente: (ON Semiconductor, 2005)

Este tipo de control de fase se recomienda solamente para circuitos con carga resistiva o levemente inductiva, (STMicroelectronics, 2008)

14.3. Calculos e implementaci ´ | on´

### 14.3.1. Rama RC de control analogico ´

Criterios de disenõ

CT = 330 nF

VˆDIAC = 32 V, (STMicroelectronics, 2018)

f = 50 Hz

Desarrollo de formulas ´

Las siguientes formulas se desarrollan teniendo en cuenta el circuito de la Figura 26. El objetivo es ´
obtener el valor maximo de la resistencia variable ´ | RT para el cual se obtiene una tension pico en el capacitor ´
CT equivalente a la tension de disparo del DIAC ´ | D.

VDIAC = IRMSXCT
(32)

IRMS =

VCA
|Z|

= q

VCA

RT

2 + XCT

2

(33)

Reemplazando la Ecuacion (33) en la Ecuaci ´ | on (32): ´

VDIAC = q

VCA

RT

2 + XCT

2

XCT
(34)

Teniendo en cuenta que:

Vˆ
DIAC =

VDIAC
√
2

(35)

Se obtiene:

Vˆ
DIAC =

√
q

2VCAXCT

RT

2 + XCT

2

(36)

La cual se desarrolla hasta obtener la siguiente ecuacion: ´

RT =

1

2πfC s
2VCA

2
Vˆ 2
DIAC
− 1 | (37)

Reemplazando valores para obtener el valor de la resistencia:

RT =

1
2π · 50 Hz · 330 nF

·

s
2 · (48 V)²
(32 V)²
− 1 = 18,04 kΩ | (38)
Se establece una resistencia mínima R4 = 470 Ω y se utiliza un potenciometro ´ | R3 = 100 kΩ. Para
obtener el rango desde la resistencia mínima a la calculada con el potenciometro, se decide agregar una ´ resistencia en paralelo R1 con el mismo, la cual se calcula a continuacion: ´
R1 ∥ R3 = R − R4 | (39)

Reemplazando valores:

(R1)⁻¹ + (100 kΩ)⁻¹

−1
= 18,04 kΩ − 470 Ω | (40)
R1 = 21,31 kΩ ≈ 22 kΩ | (41)
Debido a la tolerancia de los componentes y al hecho de que estos calculos son sobre una simplificaci ´ | on´
del circuito real (solo una rama RC), este valor representa un punto de inicio. En la practica, el valor de ´
RT optimo se mide en ´ | 21 kΩ, lo que significa una R1 = 26,58 kΩ. A causa de que los potenciometros ´
utilizados tienen una resistencia maxima significativamente menor a la especificada por el fabricante, el ´ mejor resultado se obtuvo con una R1 = 33 kΩ.

### 14.3.2. Circuito detector de cruce por cero (ZCD)

El control de fase explicado anteriormente puede ser reemplazado por un control digital, prescindiendo de la rama RC y del DIAC del circuito de la Figura 26. El control digital se compone de dos circuitos distintos: el Zero Crossing Detector (detector de cruce por cero) mostrado en la Figura 28 y el driver de TRIAC Figura 30.

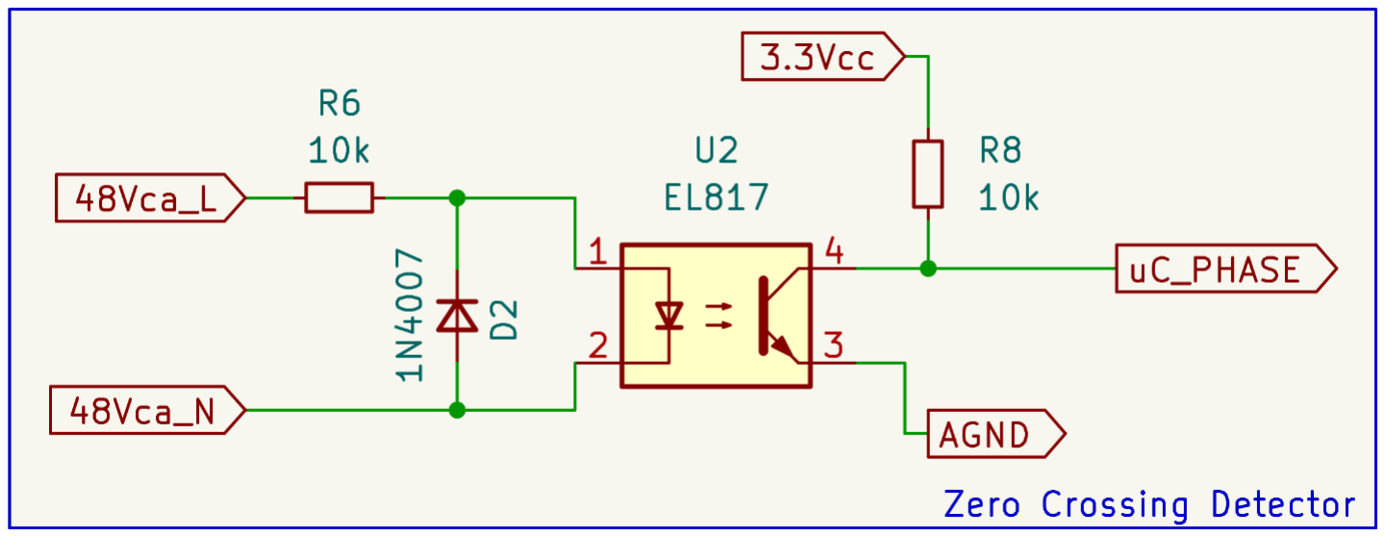
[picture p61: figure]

Figura 28: Circuito detector de cruce por cero utilizado.

Este simple circuito convierte la senal de entrada de CA sinusoidal en una se ˜ | nal aislada cuadrada, que ˜
permite al microcontrolador conocer el momento exacto de cruce por cero. De esta forma, el microcontrolador puede sincronizar el disparo de la gate del TRIAC segun el tiempo transcurrido desde el cruce por ´
cero. En la Figura 29 se observan las senales de ˜ | 48 V de CA de entrada y la de 0 V a 3,3 V de CC de salida
(amplificada para poder visualizarla).

Figura 29: Entrada y salida del detector de cruce por cero (ZCD).

En el semiciclo positivo de la senal de entrada de CA, se enciende el led interno del optoacoplador, que ˜ polariza el transistor de salida, llevando la tension´ uCphase de 3,3 V a 0 V. En el semiciclo negativo, la
corriente fluye por el diodo D2, manteniendo la tension reversa del led interno fija y menor a la m ´ | axima ´
permitida (6 V para el EL817), (Everlight, 2018)

Criterios de disenõ

IF(max) = 60 mA, (Everlight, 2018)

VF(typ) = 1,2 V, (Everlight, 2018)

Desarrollo de formulas ´

Para poder utilizar resistencias de 0,25W, se calcula primero la resistencia mínima a colocar:

Rmin =

VCA

2

Pmax

=

48 V²

0,25W

= 9,2 kΩ =⇒ R6 = 10 kΩ | (42)

Se verifica entonces que el valor de resistencia seleccionado cumpla con los criterios de diseno: ˜

IF =

VCA
R6

=

48 V
10 kΩ = 4,8 mA < 60 mA | (43)

La resistencia R8 es simplemente de pull-up para la senal que va al microcontrolador, por lo que se ˜ establece arbitrariamente R8 = 10 kΩ. Puede reducirse a valores menores hasta 1 kΩ en caso de presentar problemas.

Se debe agregar un diodo D2 en antiparalelo con la entrada del optoacoplador debido a que el mismo
tiene una tension de reversa de ´ | 6 V, lo cual es sustancialmente baja. Se opta por el 1N4007 porque es uno de
los diodos mas comunes encontrados en diversos dispositivos electr ´ | onicos, pero cualquier diodo que tenga ´
la capacidad de conmutar a 50 Hz y soporte una tension reversa de ´ | 48 V√
2 ≈ 68 VP puede utilizarse.

### 14.3.3. Driver de TRIAC

Como el microcontrolador se encuentra aislado galvanicamente del circuito de corriente alterna del ´
TRIAC y la carga, se disena un simple ˜ | driver con un optoacoplador con salida TRIAC MOC3021M, (ON
Semiconductor, 2023).

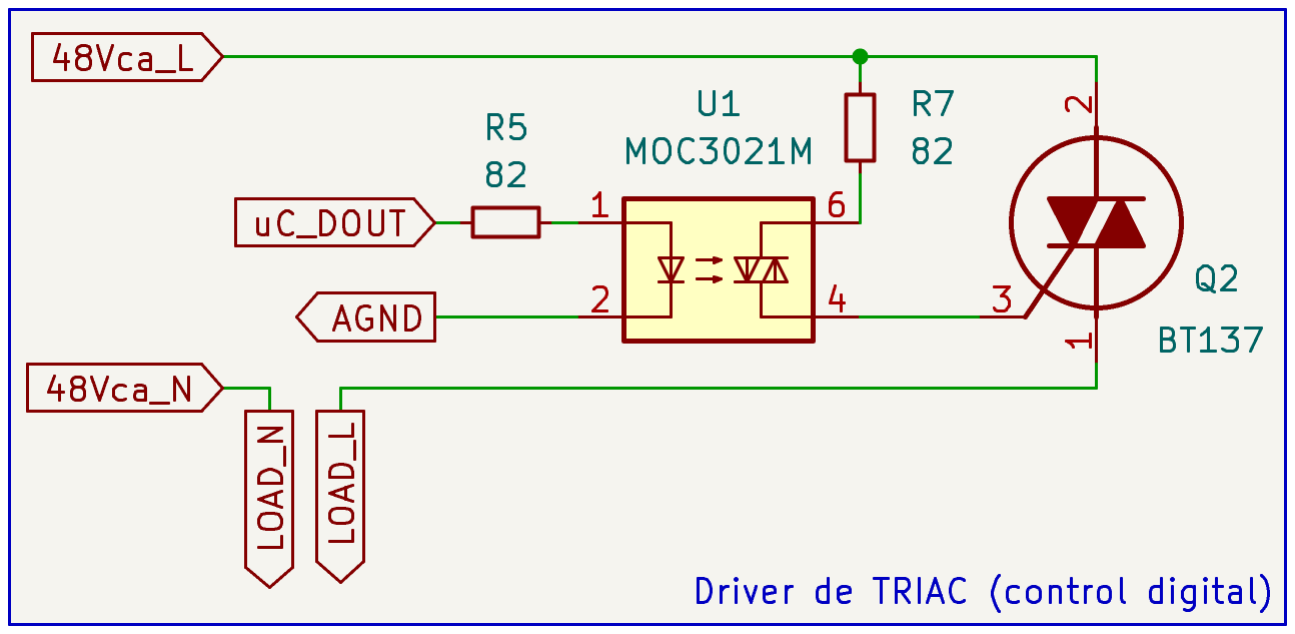
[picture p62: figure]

Figura 30: Circuito driver de TRIAC con control digital.

El fin de este circuito es disparar la gate del TRIAC con la senal del microcontrolador. Solamente es ˜ necesario calcular resistencias limitadoras de corriente para el uso correcto del optoacoplador:

Criterios de diseno - Emisor ˜

IF(max) = 60 mA =⇒ IF = 30 mA, (ON Semiconductor, 2023)

VF(typ) = 1,15 V, (ON Semiconductor, 2023)

Desarrollo de formulas - Emisor ´

R5 =

VUCdout − VF(typ)
IF

=

3,3 V − 1,15 V
30 mA | = 71,6 Ω ≈ 82 Ω | (44)

Criterios de diseno - Detector ˜

IT SM(max) = 1 A =⇒ IT SM = 0,8 A (corriente pico repetitiva maxima), (ON Semiconductor, ´ 2023)

Desarrollo de formulas - Detector ´

R7 =

Vˆ
ca
IT SM

=

Vca ·

√
2

IT SM

=

48 V ·

√
2
0,8 A | = 84,85 Ω ≈ 82 Ω | (45)
No es necesario tener en cuenta la disipacion de potencia de la resistencia ´ | R7 ya que, una vez disparada
la gate, la corriente disminuye sustancialmente.

### 14.3.4. Driver de relé

Para poder intercambiar entre ambos modos de control, el analogico y el digital, se dise ´ | na un simple ˜
circuito con un rele en la ´ | gate del TRIAC. En el contacto normal-cerrado, el rele conecta la ´ | gate del TRIAC
con la salida del DIAC perteneciente al circuito de control analogico; mientras que en el contacto normal- ´ abierto, conecta la gate con la salida del optoacoplador del circuito de control digital.

Figura 31: Circuito seleccionador de control analogico-digital. ´

En la Figura 31 se observa el circuito que permite conmutar el rele para cambiar entre ambos modos de ´
control (analogico y digital). Cuando ´ | uCRelay = 0 V, el circuito utilizado es el de control analogico, cuando ´
uCRelay = 3,3 V, se activa el control digital.

Criterios de disenõ

IL = IC = 72 mA, (Songle Relay, 2016)

βmin = 200 ; βmax = 450, (On Semiconductor, 2024)

VBE = 0,72 V, (On Semiconductor, 2024)

Desarrollo de formulas ´

Se calcula un beta promedio para el transistor:

βavg =

βmin + βmax
2

=

200 + 450
2
= 325 | (46)

Aplicando ley de las tensiones de Kirchhoff:

VUC =

IC

βavg

- R2 + VBE | (47)

Despejando R2:

R2 =

(VUC − VBE) · βavg
IC

=

(3,3 V − 0,72 V) · 325
72 mA | = 11,65 kΩ ≈ 12 kΩ | (48)

Como en el Apartado 14.3.2, se elige el 1N4007 como diodo flyback para la bobina del rele.´

### 14.3.5. Red Snubber

Es imperativo implementar algun m ´ | etodo para restringir la tasa de aumento de la tensi ´ | on reaplicada ´
del TRIAC a un valor que permita la desactivacion del TRIAC en condiciones de carga inductiva, (ON ´ Semiconductor, 2005).
Un metodo com ´ | unmente aceptado para mantener la ´ | dv/dt de conmutacion dentro de niveles tolerables ´
es utilizar una red Snubber RC en paralelo con los terminales principales del TRIAC. Dado que la tasa de aumento de la tension aplicada en los terminales del TRIAC depende de la impedancia de carga y de la ´ red Snubber RC, el circuito puede evaluarse en las peores condiciones de temperatura de funcionamiento y corriente principal maxima. Los valores de resistencia y capacitancia en red Snubber se ajustan para que ´
la tasa de aumento de la tension´ dv/dt de conmutacion se encuentre dentro del l ´ | ímite mínimo especificado
en cualquiera de las condiciones mencionadas anteriormente. El valor de la resistencia de Snubber debe ser lo suficientemente alto como para limitar las corrientes de descarga de la capacitancia de Snubber du-
rante el encendido y amortiguar la oscilacion del LC durante la conmutaci ´ | on. Generalmente, se prefiere la ´
combinacion de valores de Snubber con la mayor resistencia y la menor capacitancia que proporcione un ´ funcionamiento satisfactorio, (ON Semiconductor, 2005).

(a) Rama RC Snubber implementada

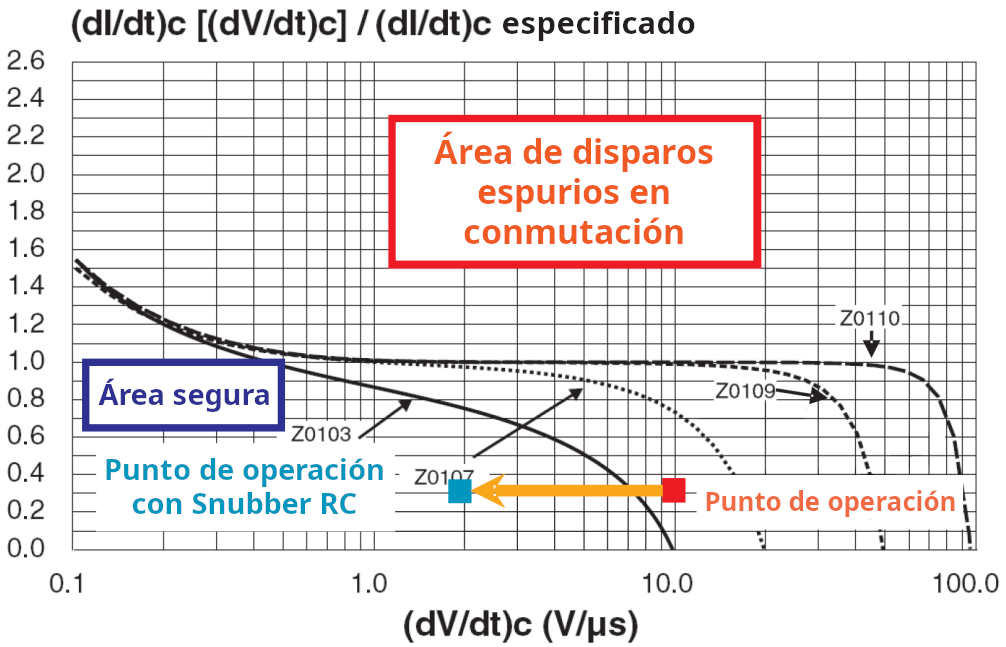
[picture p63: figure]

(b) Curva (dI/dt)c segun (dV/dt)c para TRIACs Z01, con y sin red Snubber. ´ Fuente: (STMicroelectronics, 2024)

Figura 32: Características de la red Snubber en TRIACs

En la Figura 32b se observa la tasa crítica de disminucion de la corriente de conmutaci ´ | on en estado activo ´
((dI/dt)c) respecto a la tasa crítica de aumento de la tension de conmutaci ´ | on en estado inactivo ((dV/dt)c), ´
(STMicroelectronics, 2024). Se aprecia que, en el caso de la curva con el TRIAC Z0103, el punto de ope-
racion se encuentra en la ´ | area de disparos espurios, lo cual se soluciona con la implementaci ´ | on de una red ´
Snubber.

Se selecciona una resistencia de 51 Ω y un capacitor de 10 nF ya que una red RC de estas características suele ser suficiente para evitar disparos espurios, (STMicroelectronics, 2024).

### 14.4. Disipacion de potencia en TRIAC ´

Los calculos correspondientes a la disipaci ´ | on de potencia y temperatura de juntura del TRIAC se realizan ´
siguiendo un informe de aplicacion de Philips Semiconductors, (Philips Semiconductors, 2005). ´

Teniendo en cuenta:

Corriente de TRIAC RMS IT(RMS) = 1 A (maximo establecido del m ´ | odulo) ´

Tension de encendido del TRIAC ´ | Vo = 1,264 V, (WeEn Semiconductors, 2018)

Resistencia de pendiente del TRIAC Rs = 0,038 Ω, (WeEn Semiconductors, 2018)
Resistencia de juntura-ambiente del TRIAC Rth(j−a) = 60 K/W = 60 ◦C/W, (WeEn Semiconduc-

tors, 2018)
Temperatura de ambiente maxima ´ | Ta(max) = 40 ◦C
Temperatura de juntura maxima del TRIAC ´ | Tj(max) = 125 ◦C, (WeEn Semiconductors, 2018)

Se calcula la corriente promedio de carga:

IT(AV E) =

2 ×

√
2 × IT(RMS)
π

=

2

√
21 A
π
= 0,9 A | (49)

Luego se calcula la potencia disipada por el TRIAC:

P = Vo × IT(AV E) + Rs × IT(RMS)

2 = 1,264 V × 0,9 A + 0,038 Ω × (1 A)² = 1,18W | (50)

Finalmente se puede calcular la temperatura de juntura del TRIAC en operacion: ´

Tj = Ta + P × Rthj−a = 40 ◦C + 1,18W × 60

◦C

W

= 110,8

◦C < 125 ◦C | (51)

Por lo tanto, no es necesario colocar un disipador en el TRIAC, ya que la temperatura de juntura calcu-
lada se encuentra por debajo del maximo especificado por el fabricante bajo las condiciones de operaci ´ | on´
establecidas.

### 14.5. Simulacion´

Para verificar el correcto funcionamiento del circuito control de fase analogico del Apartado 14.3.1, se ´ realiza una simple simulacion con el software gratuito LTspice, (Analog Devices, 2025). ´

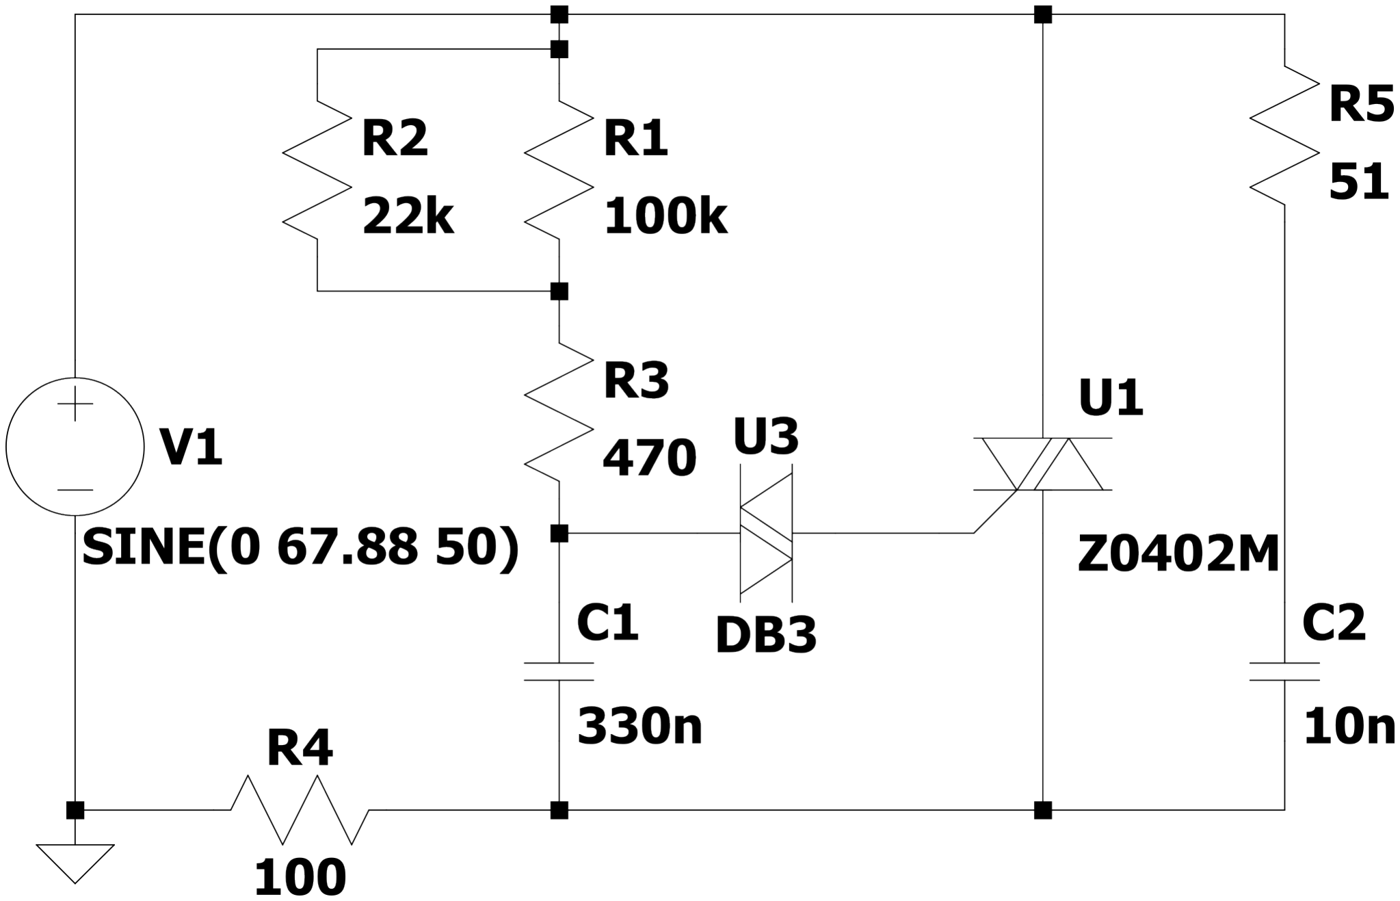
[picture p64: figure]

Figura 33: Circuito en LTspice⁶

6
Se utiliza el TRIAC Z0402M por disponibilidad de modelo de simulacion. Sus caracter ´ | ísticas son similares a las del BT137.

(a) Resistencia R3 = 0,01 Ω | (b) Resistencia R3 = 50 kΩ
(c) Resistencia R3 = 100 kΩ

Figura 34: Resultados de la simulacion´

Como se observa en la Figura 34, el circuito se comporta segun lo esperado, cambiando el ´ | angulo de ´
disparo del TRIAC con distintos valores de resistencia del potenciometro. La simulaci ´ | on comienza a los ´
40 ms para visualizar el comportamiento del circuito en regimen permanente. ´

## 15. Modulo inversor de onda cuadrada ´

La funcion de un inversor es cambiar un voltaje de entrada de corriente continua (DC) a un voltaje ´ simetrico de salida de corriente alterna (CA) de magnitud y frecuencia deseadas. El voltaje de salida puede ´ ser fijo o variable a una frecuencia tambien fija o variable. Se puede obtener un voltaje de salida variable si ´ se varía el voltaje de DC de entrada y se mantiene constante la ganancia del inversor. Por otra parte, si el voltaje de entrada de DC es fijo y no es controlable, se puede obtener un voltaje de salida variable si se hace que la ganancia del inversor varíe, lo que normalmente se consigue mediante el control de modulacion por ´ ancho de pulso (PWM) dentro del inversor. La ganancia del inversor se puede definir como la relacion del ´ voltaje de salida de CA al voltaje de entrada de DC.

Las formas de onda del voltaje de salida de los inversores ideales deben ser senoidal. Sin embargo, los circuitos mas simples de inversores generan una onda de salida cuadrada lo cual es suficiente para algunas ´

aplicaciones sencillas.

Para aplicaciones de baja y mediana frecuencia, se pueden aceptar voltajes de onda cuadrada o de onda cuasi cuadrada; para aplicaciones de alta potencia, se requieren formas de onda senoidales poco distorsionadas, (Rashid, 2015).

Para operar correctamente el inversor, se deben cumplir las siguientes reglas:

1. Los interruptores de la misma rama no pueden estar encendidos simultaneamente, ya que se produce ´
un cortocircuito a traves de la fuente de tensi ´ | on de continua. ´
2. Debe colocarse un diodo en antiparalelo con cada interruptor para proporcionar un camino de corriente a las cargas inductivas. Si el interruptor comercial ya incluye este diodo, entonces el circuito está completo.
3. En la implementacion pr ´ | actica, debe considerarse un tiempo muerto (tambi ´ | en conocido como tiempo ´
de bloqueo) en las senales de control de los interruptores de la rama, para evitar la violaci ˜ | on de la ´
regla 1.

(Rashid, 2024)

15.1. Interaccion del usuario: control y verificaci ´ | on experimental ´
El modulo inversor de onda cuadrada est ´ | a dise ´ | nado para que el usuario pueda ajustar la frecuencia de ˜
la senal de salida mediante un potenci ˜ | ometro ubicado en la propia placa, sin requerir interacci ´ | on con la ´
pantalla central del sistema. Para la verificacion experimental, se recomienda utilizar un osciloscopio para ´ visualizar la onda cuadrada generada por el temporizador 555, la cual oscila entre 0 V a 12 V.

Al medir la tension en la carga, se observa una onda cuadrada alternando entre valores positivos y ne- ´ gativos (aproximadamente 4,5 V a −4,5 V), producto de la topología de medio puente. Girando el poten-
ciometro, el usuario puede modificar la frecuencia de la se ´ | nal y observar los cambios en tiempo real en el ˜
osciloscopio, permitiendo así la experimentacion y ajuste fino del funcionamiento del inversor. ´

### 15.2. Descripcion de funcionamiento de un oscilador 555 ´

El circuito integrado IC555 es un dispositivo de temporizacion de precisi ´ | on muy econ ´ | omico, popular y ´
util, que puede funcionar como un temporizador simple para generar pulsos ´ | unicos o retardos largos, o como ´
un oscilador que produce una serie de formas de onda estabilizadas con ciclos de trabajo variables del 50 % a 100 %.

El IC555 es un dispositivo de 8 pines extremadamente robusto y estable, que puede operar con gran precision en modo monoestable, biestable o astable. Esto le permite ser utilizado en una amplia variedad ´ de aplicaciones, como temporizadores de un solo disparo o con retardo, generacion de pulsos, fuentes de ´ alimentacion, convertidores, entre otros. En realidad, puede utilizarse en cualquier circuito que requiera ´
algun tipo de control de tiempo, ya que sus aplicaciones son pr ´ | acticamente ilimitadas. ´
El uso mas com ´ | un del dispositivo es como oscilador en modo astable, conectando dos resistencias y ´
un capacitor a sus terminales para generar un tren de pulsos con un período de tiempo determinado por la constante de tiempo de la red RC, como se puede ver en la Figura 35.

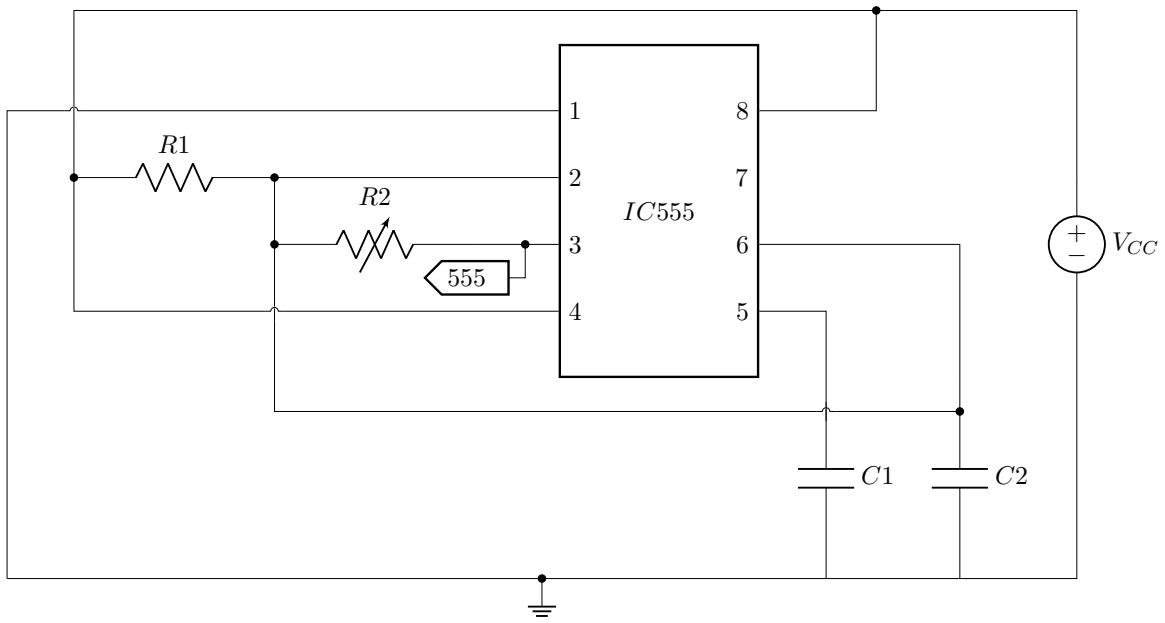
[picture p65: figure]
+ VCC

Figura 35: Circuito oscilador astable.

En configuracion astable requiere que el IC se dispare continuamente tras cada ciclo de temporizaci ´ | on. ´
Este reinicio se logra conectando juntos la entrada de disparo (pin 2) y la entrada de umbral (pin 6), permitiendo que el dispositivo funcione como un oscilador astable. Así, un oscilador 555 no tiene estados estables, ya que cambia continuamente de un estado al otro.

Para que produzca un ciclo de trabajo del 50 %, el capacitor de temporizacion, conectado al pin 6, se ´ tiene que cargar y descargar a traves de la resistencia R2 (variable). ´

Cuando la salida esta en ALTO, el capacitor se carga a trav ´ | es de R2, y cuando la salida est ´ | a en BAJO, el ´
capacitor se descarga a traves de R2. La resistencia R1 tiene un valor alto y se utiliza para garantizar que el ´
capacitor se cargue completamente hasta alcanzar el mismo valor que la tension de alimentaci ´ | on. ´

El reset (pin 4) debe conectarse a VCC para evitar que el circuito se desactive involuntariamente, mientras que el control de voltaje (pin 5) se conecta con un capacitor de bajo valor a tierra para mejorar la estabilidad y reducir el ruido. El pin 7 (Descarga) no se usa en esta configuracion, ya que la carga y descarga del ´ capacitor ocurren exclusivamente a traves de la resistencia R2, (Electronics Tutorials, 2013). ´

### 15.3. Descripcion de funcionamiento de un inversor de medio puente ´

Como se menciona anteriormente, un inversor es un convertidor que transfiere potencia desde una fuente
de continua a una carga de alterna. La funcion de un inversor es, entonces, cambiar la tensi ´ | | on de entrada ´
de corriente continua en una tension sim ´ | etrica de salida en corriente alterna con una magnitud, frecuencia y ´
fase deseada.
En inversores monofasicos se utilizan dos topolog ´ | ías basicas: medio puente Figura 36, el utilizado en ´
este caso, y puente completo. La principal desventaja de utilizar un inversor de medio puente es que se obtiene solo la mitad de la tension que se proporciona en la entrada. ´

Figura 36: Circuito de inversor medio puente.

En este circuito tenemos dos etapas, una de potencia en la cual encontramos el medio puente conformado por dos transistores MOSFET y dos capacitores electrolíticos, y una etapa de control que depende del oscilador 555 visto anteriormente.

### 15.3.1. Etapa de control

El control del medio puente se realiza a traves de la se ´ | nal de salida del oscilador 555, que se divide en ˜
dos ramas. Una de estas ramas se conecta a la gate del transistor Q1 mediante una resistencia, mientras que
la otra rama lo hace a la base de un transistor BJT, tambien a trav ´ | es de una resistencia. ´

La gate del transistor Q2 se conecta al colector del transistor BJT, que tiene una resistencia conectada a
la tension de alimentaci ´ | on´ VCC. El emisor del BJT esta conectado a tierra. Este transistor BJT act ´ | ua como ´
una compuerta NOT: cuando el oscilador proporciona un impulso alto en la base del BJT, este coloca la gate de Q2 a tierra, evitando que Q2 conduzca. Al mismo tiempo, la gate de Q1 recibe la tension´ VCC, lo que hace que Q1 conduzca.

Cuando la salida del oscilador pasa a un impulso bajo, el comportamiento se invierte. Q1 deja de conducir
porque no recibe tension en su ´ | gate. Esto tambien ocurre en el BJT, que deja de conducir, y la tensi ´ | on´ VCC
aplicada a su colector se dirige a la gate de Q2, haciendo que Q2 conduzca.

Así, se logra que solo uno de los dos MOSFETs conduzca en cada ciclo de conmutacion, lo que genera ´ la accion complementaria. ´

### 15.3.2. Acople

El uso de un amplificador operacional como seguidor de tension entre la salida del IC555 y la etapa ´ de potencia resulta conveniente porque actua como adaptador de impedancia, presentando alta impedancia ´ de entrada y baja impedancia de salida. De esta manera, evita que el IC deba excitar cargas capacitivas directamente, mejora la forma de onda entregada y asegura niveles de tension m ´ as estables. ´

−

+

MOSF ET s
IC555

Figura 37: Seguidor de tension. ´

### 15.3.3. Etapa de potencia

Los capacitores electrolíticos conforman un divisor de tension y estos se mantienen cargados gracias a la ´ tension entregada por el regulador. ´

Cuando la salida del oscilador esta en ALTO, como mencionamos, Q1 se activa y Q2 no lo hace. Al ´ activarse Q1 la tension que otorga el capacitor C1 aplicada en la carga, y el sentido de la corriente es el ´ siguiente:

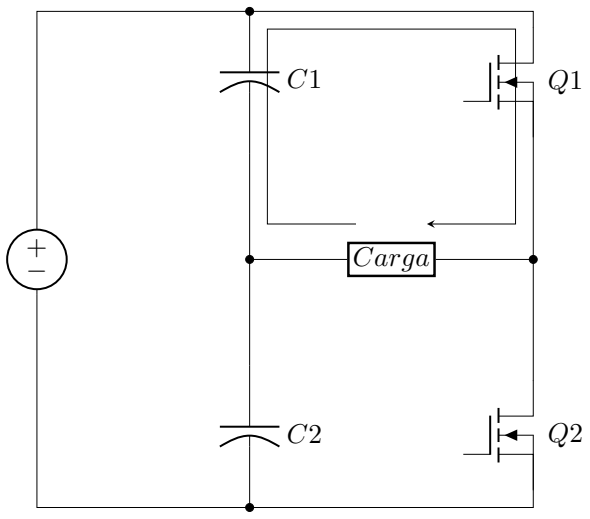
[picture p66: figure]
Carga −

Figura 38: Conmutacion 1. ´

Cuando el oscilador pasa a estado BAJO, ahora el que se activa es Q2 y ya no lo hace Q1. En este caso
la tension de C2 se aplica en la carga y es negativa ya que la corriente circula en direcci ´ | on opuesta: ´

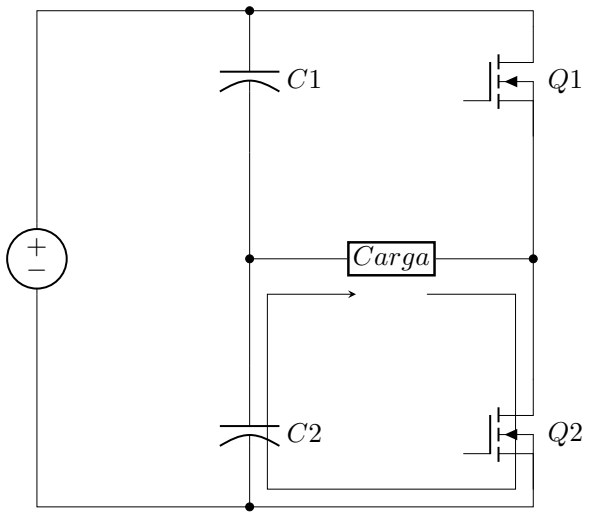
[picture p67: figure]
Carga −

Figura 39: Conmutacion 2. ´

Las graficas correspondiente a cada estado de conmutaci ´ | on, se muestran en la Figura 40. ´

Q1

Q2

Carga

Amplitud

t

t

t

Figura 40: Forma de onda.

Las dos primeras formas de onda muestran los pulsos aplicados a los MOSFET, donde cada uno recibe el
pulso cuando el interruptor complementario esta desactivado. El tercer gr ´ | afico muestra la forma de onda de ´
voltaje a traves de la carga. Esto muestra que la polaridad del voltaje cambia con respecto a la conmutaci ´ | on. ´

### 15.4. Calculos ´

### 15.4.1. Temporizador 555 configurado como oscilador con ciclo de trabajo del 50 %

Durante cada ciclo, el capacitor se carga hasta el límite superior del comparador

| 2 3 × VCC a traves del ´
resistor externo R2 y el capacitor C1, y luego se descarga hasta el límite inferior del comparador
| 1 3 × VCC

a traves de los mismos componentes, (Scandy & Jones, 2021). ´

La ecuacion del voltaje del capacitor en un circuito RC es: ´

VCAP(t) = V

1 − e

−t/RC
(52)

Reorganizando para obtener el tiempo de carga desde 1

3 × VCC hasta 2
3 × VCC:

tcarga = −RC × ln
1 −

VCAP
V
(53)

Si V = VCC, VCAP(t1) = 1
3

VCC y VCAP(t2) = 2
3

VCC, se obtiene:

tcarga = t2 − t1 = −RC × ln 1
3

+ RC × ln
2
3
(54)

Simplificando:

tcarga = 0,693 × RC | (55)

Los tiempos de carga y descarga son iguales:

tdescarga = 0,693 × RC | (56)

Por lo que la frecuencia resultante es:

f =

1

tcarga + tdescarga

=

1
2 × 0,693 × RC | (57)
Por criterio de diseno, se toma ˜ | C = 0,1 µF y f = 50 Hz, la resistencia resultante es:

R =

1
2 × 0,693 × 50 Hz × 0,1 µF
= 144,3 kΩ | | (58)

Ya que no es un valor comercial, se emplea una resistencia de 120 kΩ en serie con un potenciometro de ´ 100 kΩ, para tener un ajuste preciso de la frecuencia deseada. Ademas, se utiliza una resistencia adicional ´ R1 de 3,9 MΩ para asegurar la carga completa del capacitor, y así un ciclo de trabajo del 50 %. Este valor de resistencia es el que mejores resultados entrega en las pruebas realizadas. En cuanto a la alimentacion´
del integrado, se utiliza la tension proporcionada por el m ´ | odulo general ( ´ | 12 V de corriente continua), por lo
que entrega a la salida del mismo una onda cuadra de 0 V a 12 V.

### 15.4.2. Regulador de voltaje

El MOSFET seleccionado es el IRFZ44N, (International Rectifier, 2010), y el umbral de conduccion es ´
VGS(th) = 2 V a 4 V, por lo que la tension de alimentaci ´ | on del IC555 debe ser mayor por ´ | 3 V al de ali-
mentacion de MOSFETs, para obtener esta diferencia entre ´ | | gate y surtidor. Para ello se utiliza un regulador
KA7808, el cual se alimenta con 12 V y entrega 8 V a la salida, con los que se alimenta el surtidor del MOSFET.

15.4.3. Calculo de la capacitancia m ´ | ínima

Figura 41: Inversor medio puente con control por 555

Considerando las características del MOSFET seleccionado, teniendo una carga puramente resistiva y una frecuencia de 50 Hz, se plantea la ecuacion de descarga de un capacitor. ´

VCC = 9 V

RLOAD = 100 Ω

T = 20 ms

V (t) = V0 × e

−t/RC | (59)

La descarga completa del capacitor se da cuando Vt =

T
2

y como se menciona anteriormente, la tension´
en este modelo de inversor es la mitad de la tension de alimentaci ´ | on, ´

VCC
2

. Reescribiendo la Ecuacion (59) ´ se obtiene la Ecuacion (60) ´

V

T
2
=

VCC
2
× β | (60)

Donde β es:

β = e

− T
2RC | (61)

Aplicando logaritmo y despejando C:

ln(β) = −

T
2RC | (62)

C ≥

T
2R ln(β)

(63)

Se selecciona un β = 0,9, el cual es un valor razonable:

C ≥

20 ms
2 × 100 Ω × ln(0,9)
= 950 µF | (64)

Siendo 950 µF el valor mínimo de capacitancia. Al aumentar el valor de la misma se obtienen mejores resultados de rizado, por lo que mediante pruebas de laboratorio se establece un valor de 1500 µF.

### 15.4.4. Gate del MOSFET

La resistencia de gate del MOSFET que conecta directamente con la salida del IC555, se calcula teniendo en cuenta dos consideraciones, por un lado, el pico de corriente al momento de conducir y por otro la
corriente maxima de salida del IC555. El MOSFET tiene una ´ | Qg que ronda los 70 nC, y por criterio de
diseno, el tiempo de carga seleccionado debe estar dentro de los ˜ | 10 µs.

Qg = 70 nC, (International Rectifier, 2010)

tsw = 10 µs

Ig =

Qg

tsw

=

70 nC
10 µs
= 7 mA | (65)

Por ley de Ohm

Rg =

V
Ig

=

12 V
7 mA = 1714 Ω | (66)
Sin embargo, con una resistencia de 1,2 kΩ, se reduce el tiempo de conmutacion a ´ | 7 µs, y se mantiene la
potencia disipada por debajo de medio Watt.

### 15.4.5. Driver de MOSFET

Para intercalar el funcionamiento de los MOSFETs y que solo uno conduzca por cada oscilacion, se ´
utiliza un transistor BJT BC548, en saturacion como ´ | driver del segundo MOSFET. Se coloca entonces, una
resistencia pull-up para limitar la corriente en el colector del BC548.

VCESat = 0,2 V, (On Semiconductor, 2024)

IC = 10 mA

VBE = 0,7 V, (On Semiconductor, 2024)

Rpullup =

(VCC − VCESat )
IC

=

12 V − 0,2 V
10 mA | = 1180 Ω ≈ 1,2 kΩ | (67)

Para que el BJT opere en saturacion, la corriente de base debe ser suficiente para ”sobresaturarlo”. Para ´ calcular la resistencia de base, se aplica la ley de tensiones de Kirchhoff:

IC = 50 mA

β = 200 , (On Semiconductor, 2024)

VBE = 0,7 V, (On Semiconductor, 2024)

RB =

(V555 − VBE) · β
IC

=

(12 V − 0,7 V) · 200
50 mA | = 45,2 kΩ ≈ 47 kΩ | (68)

### 15.4.6. Disipacion de potencia en transistores ´

No se incluyen calculos de disipaci ´ | on de potencia en los transistores, dado que las condiciones de ope- ´
racion (baja corriente de carga y tiempos de conmutaci ´ | on cortos) aseguran que las p ´ | erdidas por conducci ´ | on´
y conmutacion permanecen dentro de los l ´ | ímites seguros especificados por los fabricantes.

### 15.5. Simulacion´

Para verificar el correcto funcionamiento del circuito oscilador IC555 y la tension en la carga, se realiza ´ una simple simulacion con el software gratuito LTspice, (Analog Devices, 2025). ´

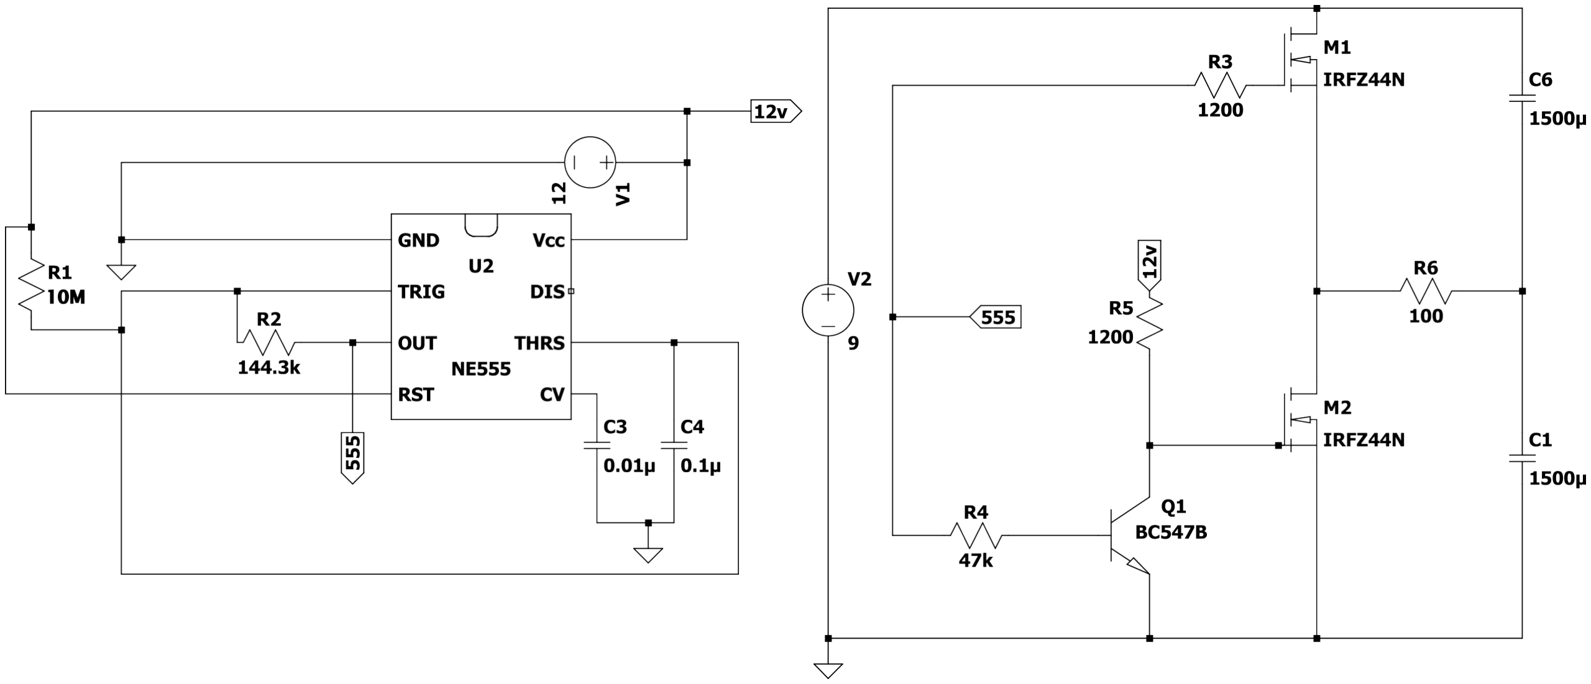
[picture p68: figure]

Figura 42: Circuito en LTspice.

(a) Senal a la salida del IC555. ˜ | (b) Senal en la carga. ˜
Figura 43: Graficos de simulaci ´ | on´

Como se observa en la Figura 43, el circuito se comporta segun lo esperado. ´

## 16. Desarrollo de Hardware

El desarrollo de hardware del proyecto implica una transicion desde el dise ´ | no te ˜ | orico de los circuitos ´
electronicos hasta la validaci ´ | on experimental de los mismos. En esta etapa, se llevan a cabo pruebas sobre ´
prototipos armados en placas experimentales perforadas, permitiendo detectar y corregir posibles errores
antes de avanzar con el diseno y fabricaci ˜ | on de las placas de circuito impreso (PCBs) finales. ´

### 16.1. Prototipado con placas experimentales perforadas

Para confirmar el correcto funcionamiento de los circuitos disenados anteriormente, se confeccionan ˜ prototipos con placas experimentales perforadas para poder realizar pruebas y correcciones de componentes con rapidez y costos mínimos. Este proceso fue fundamental para asegurar la funcionalidad y confiabilidad
del hardware desarrollado. Para minimizar el tiempo de fabricacion, se realiza su dise ´ | no en computadora ˜
anteriormente:

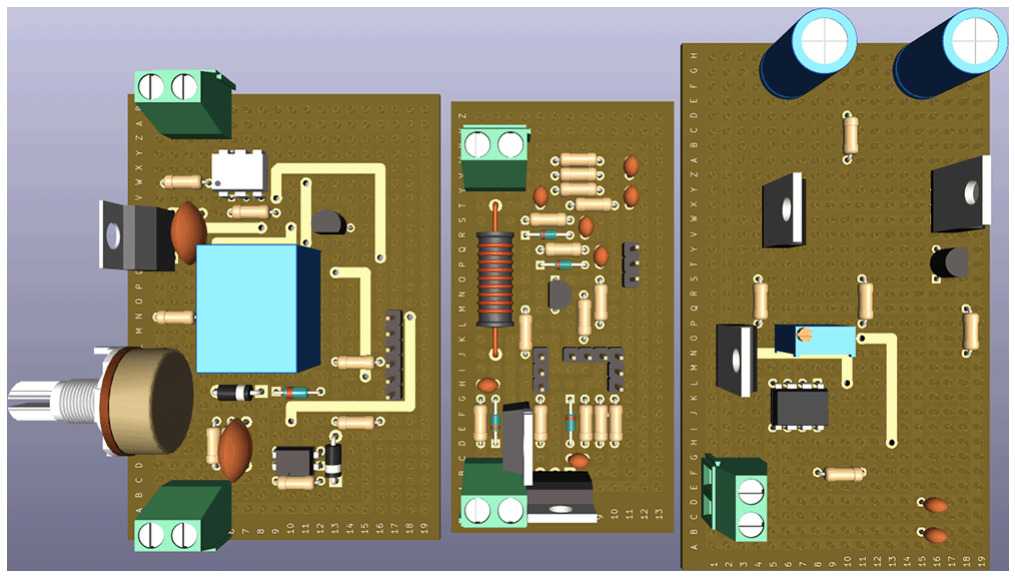
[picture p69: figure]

Figura 44: Vista frontal de los modelos 3D de las placas experimentales perforadas. De izquierda a
derecha: modulo recortador de onda, m ´ | odulo convertidor Buck, m ´ | odulo inversor de onda cuadrada ´

Los resultados obtenidos son satisfactorios, permitiendo realizar las pruebas necesarias para optimizar el circuito final. No obstante, el diseno directo de simples placas de circuito impreso (PCB) son una alternativa ˜
mas eficiente para corroborar el funcionamiento del circuito dise ´ | nado. Las placas experimentales perforadas, ˜
ademas de tener un costo significativamente mayor que las placas v ´ | írgenes de cobre, presentan problemas
de calidad, como pads de cobre que se desprenden con facilidad durante el proceso de soldadura.

### 16.2. Diseno de PCBs finales ˜

Una vez obtenidos los circuitos finales con sus respectivos valores de componentes, se procede a realizar los disenos de las PCBs necesarias para el proyecto: ˜

1. PCB Modulo recortador de onda. ´
2. PCB Modulo convertidor Buck. ´
3. PCB Modulo inversor de onda cuadrada. ´
4. Mini-PCB conector hembra PCIe x4.
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

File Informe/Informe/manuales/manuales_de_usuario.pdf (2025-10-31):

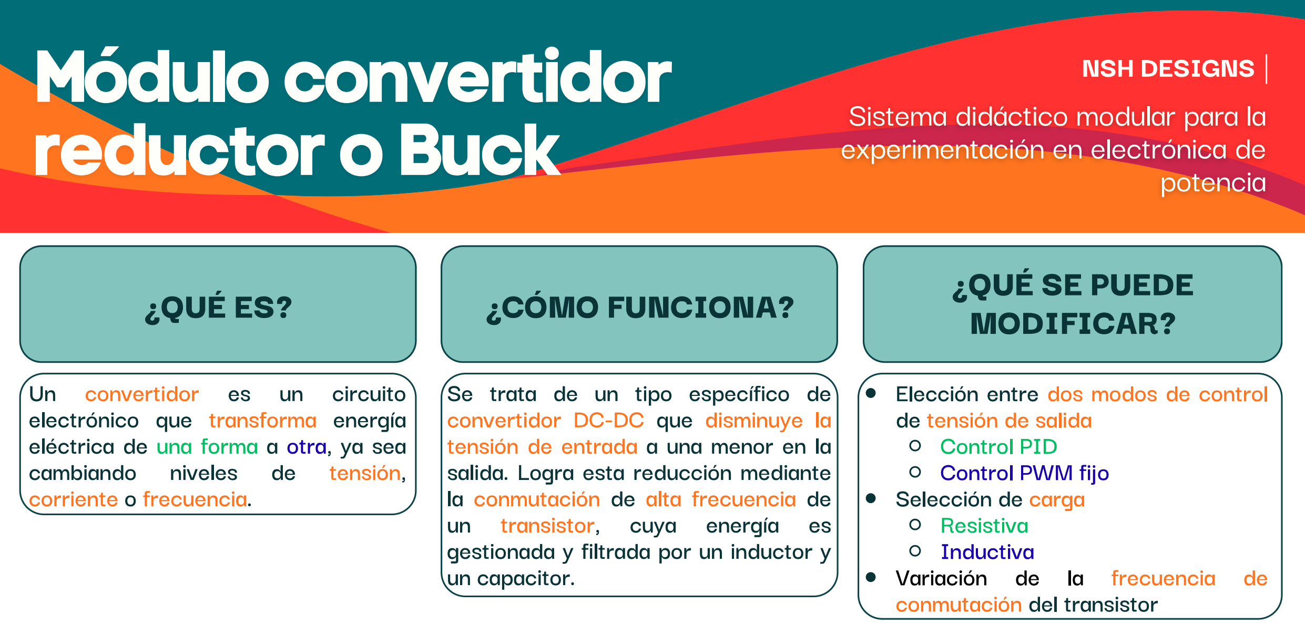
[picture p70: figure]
¿QUÉ SE PUEDE MODIFICAR?; Un convertidor es un circuito electrónico que transforma energía eléctrica de una forma a otra, ya sea cambiando niveles de tensión, corriente o frecuencia.; ¿QUÉ ES?; ¿CÓMO FUNCIONA?; Se trata de un tipo específico de convertidor DC-DC que disminuye la tensión de entrada a una menor en la salida. Logra esta reducción mediante la conmutación de alta frecuencia de un transistor, cuya energía es gestionada y filtrada por un inductor y un capacitor.; Móduloconvertidor reductoroBuck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
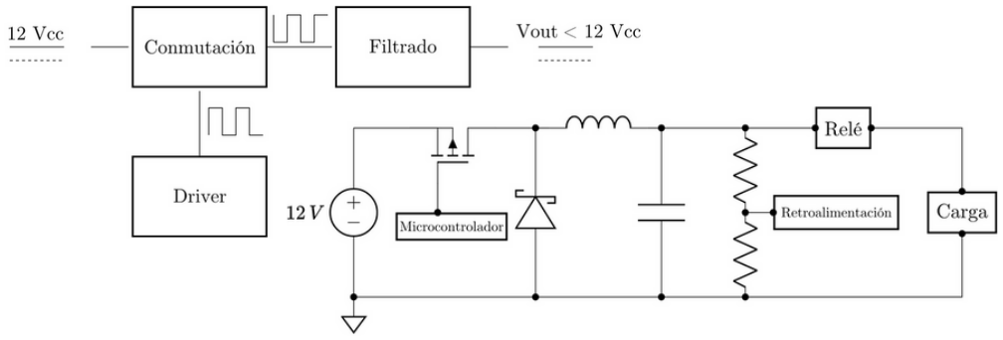
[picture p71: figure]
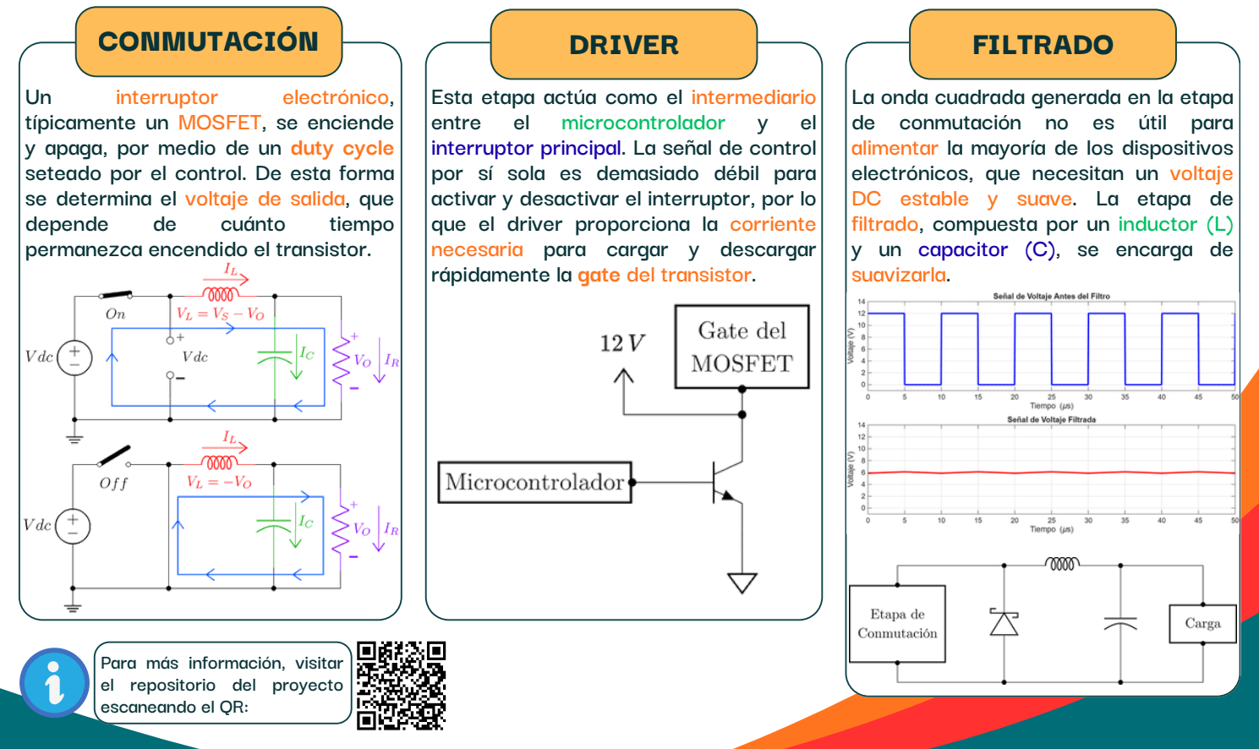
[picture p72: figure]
FILTRADO; Para más información, visitar el repositorio del proyecto escaneando el QR:; La onda cuadrada generada en la etapa de conmutación no es útil para; electrónicos, que necesitan un voltaje DC estable y suave. La etapa de filtrado, compuesta por un inductor (L) y un capacitor (C), se encarga de suavizarla.; Esta etapa actúa como el intermediario entre el microcontrolador y el; por sí sola es demasiado débil para; que el driver proporciona la corriente necesaria para cargar y descargar rápidamente la gate del transistor.; interruptor; electrónico,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

alimentar la mayoría de los dispositivos interruptor principal. La señal de control activar y desactivar el interruptor, por lo

## ¿QUÉ SE PUEDE VER?

### TENSIÓN EN

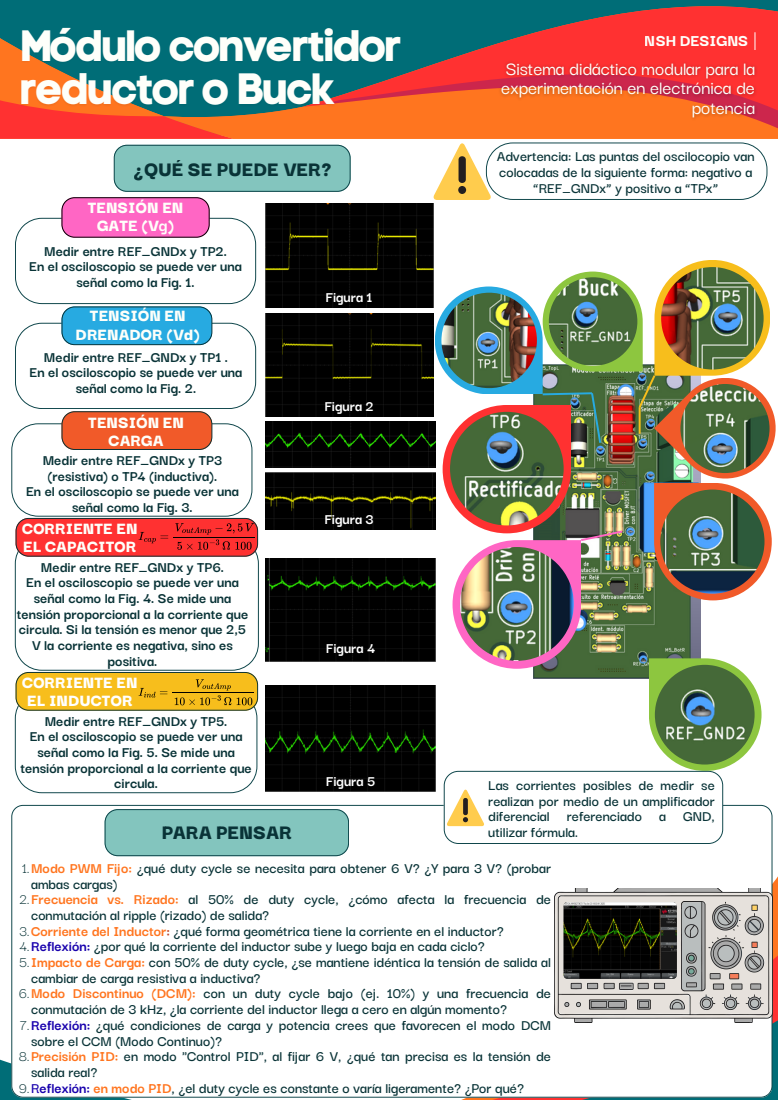
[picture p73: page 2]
Móduloconvertidor reductoroBuck; circula.; positiva.; Figura 1; Figura 2; Figura 3; Figura 4; Figura 5; Las corrientes posibles de medir se; PARA PENSAR; potencia

Advertencia: Las puntas del oscilocopio van
colocadas de la siguiente forma: negativo a
“REF_GNDx” y positivo a “TPx”

GATE (Vg)
Medir entre REF_GNDx y TP2.
En el osciloscopio se puede ver una
señal como la Fig. 1.
TENSIÓN EN
DRENADOR (Vd)
Medir entre REF_GNDx y TP1 .
señal como la Fig. 2.
CARGA

Medir entre REF_GNDx y TP3
(resistiva) o TP4 (inductiva).
señal como la Fig. 3.
CORRIENTE EN
EL CAPACITOR
Medir entre REF_GNDx y TP6.
señal como la Fig. 4. Se mide una
tensión proporcional a la corriente que
circula. Si la tensión es menor que 2,5
V la corriente es negativa, sino es
EL INDUCTOR
Medir entre REF_GNDx y TP5.
señal como la Fig. 5. Se mide una

realizan por medio de un amplificador
diferencial referenciado a GND,
utilizar fórmula.

1.Modo PWM Fijo: ¿qué duty cycle se necesita para obtener 6 V? ¿Y para 3 V? (probar
ambas cargas)
2.Frecuencia vs. Rizado: al 50% de duty cycle, ¿cómo afecta la frecuencia de
conmutación al ripple (rizado) de salida?
3.Corriente del Inductor: ¿qué forma geométrica tiene la corriente en el inductor?
4.Reflexión: ¿por qué la corriente del inductor sube y luego baja en cada ciclo?
5.Impacto de Carga: con 50% de duty cycle, ¿se mantiene idéntica la tensión de salida al
cambiar de carga resistiva a inductiva?
6.Modo Discontinuo (DCM): con un duty cycle bajo (ej. 10%) y una frecuencia de
conmutación de 3 kHz, ¿la corriente del inductor llega a cero en algún momento?
7.Reflexión: ¿qué condiciones de carga y potencia crees que favorecen el modo DCM
sobre el CCM (Modo Continuo)?
8.Precisión PID: en modo "Control PID"
salida real?
9.Reflexión: en modo PID, ¿el duty cycle es constante o varía ligeramente? ¿Por qué?

, al fijar 6 V, ¿qué tan precisa es la tensión de

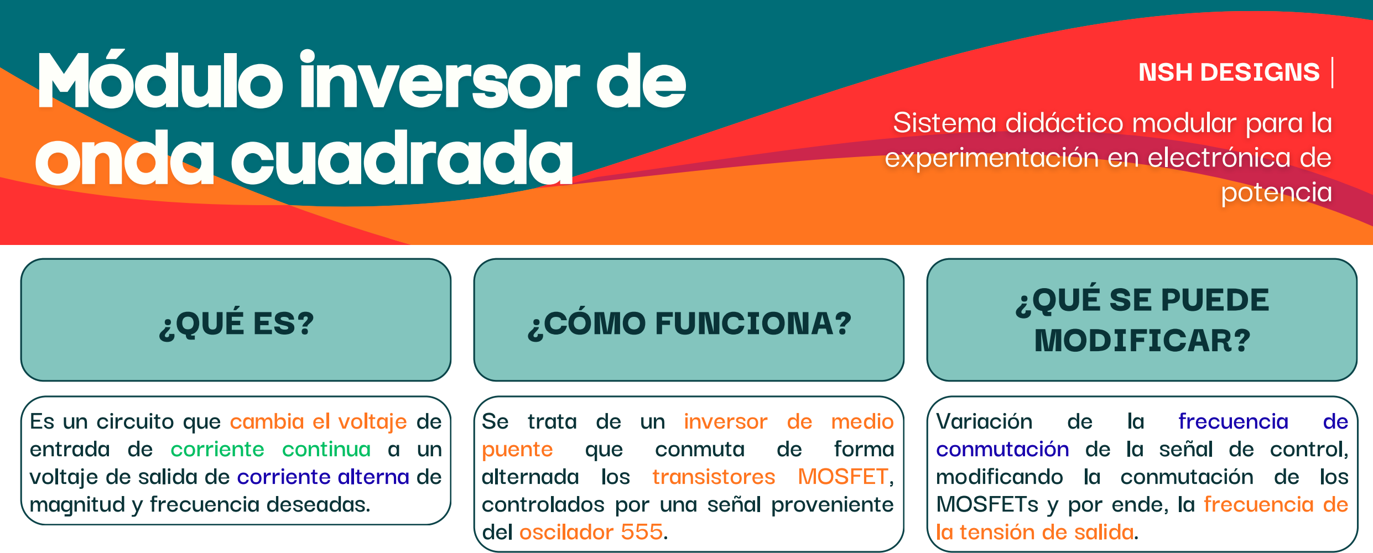
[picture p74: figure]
Es un circuito que cambia el voltaje de entrada de corriente continua a un; magnitud y frecuencia deseadas.; ¿QUÉ ES?; ¿CÓMO FUNCIONA?; Se trata de un inversor de medio puente que conmuta de forma alternada los transistores MOSFET, controlados por una señal proveniente del oscilador 555.; ¿QUÉ SE PUEDE MODIFICAR?; Variación de la frecuencia de conmutación de la señal de control, modificando la conmutación de los MOSFETs y por ende, la frecuencia de la tensión de salida.; Móduloinversorde ondacuadrada; potencia

voltaje de salida de corriente alterna de

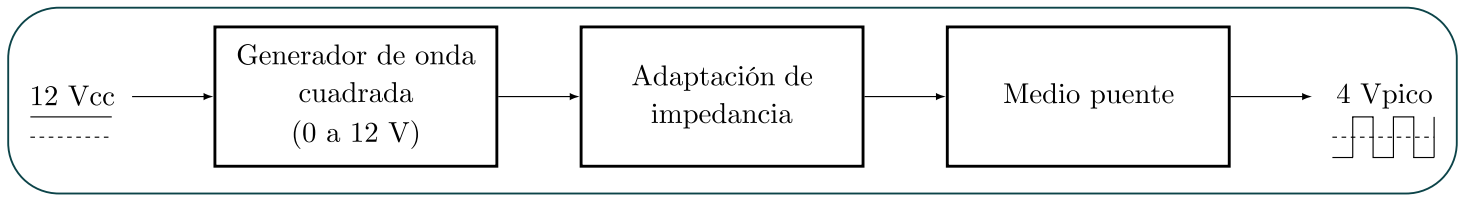
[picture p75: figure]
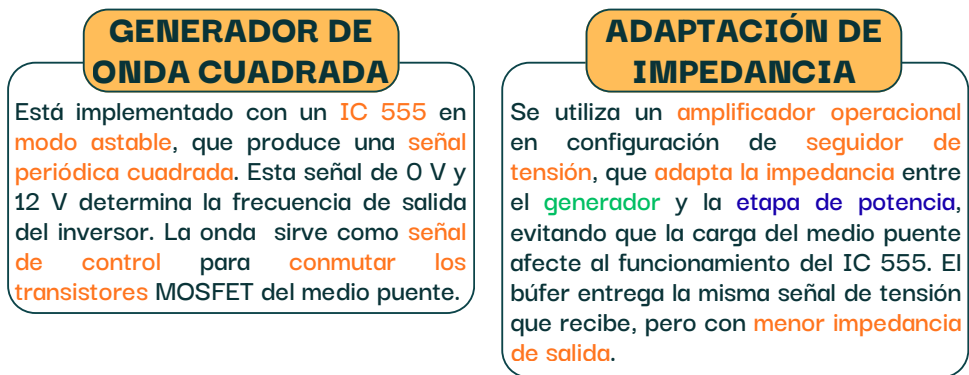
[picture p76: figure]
Está implementado con un IC 555 en modo astable, que produce una señal periódica cuadrada. Esta señal de 0 V y 12 V determina la frecuencia de salida del inversor. La onda sirve como señal de control para conmutar los transistores MOSFET del medio puente.; Se utiliza un amplificador operacional en configuración de seguidor de tensión, que adapta la impedancia entre el generador y la etapa de potencia, evitando que la carga del medio puente afecte al funcionamiento del IC 555. El búfer entrega la misma señal de tensión que recibe, pero con menor impedancia de salida.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
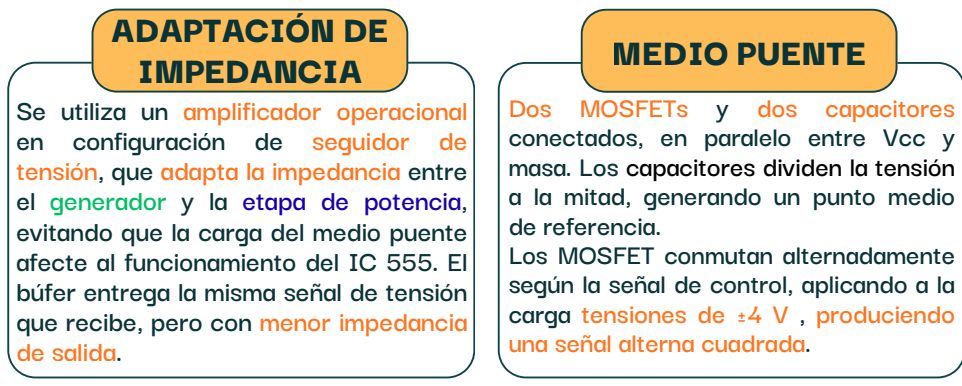
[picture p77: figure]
Dos MOSFETs y dos capacitores conectados, en paralelo entre Vcc y; a la mitad, generando un punto medio de referencia. Los MOSFET conmutan alternadamente; carga tensiones de ±4 V , produciendo una señal alterna cuadrada.; MEDIO PUENTE ADAPTACIÓN DE
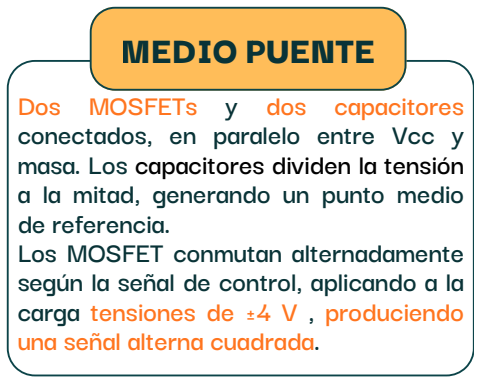
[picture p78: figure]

Salida del medio puente: 4 Vpico, medida sobre una carga puramente resistiva.

masa. Los capacitores dividen la tensión

según la señal de control, aplicando a la

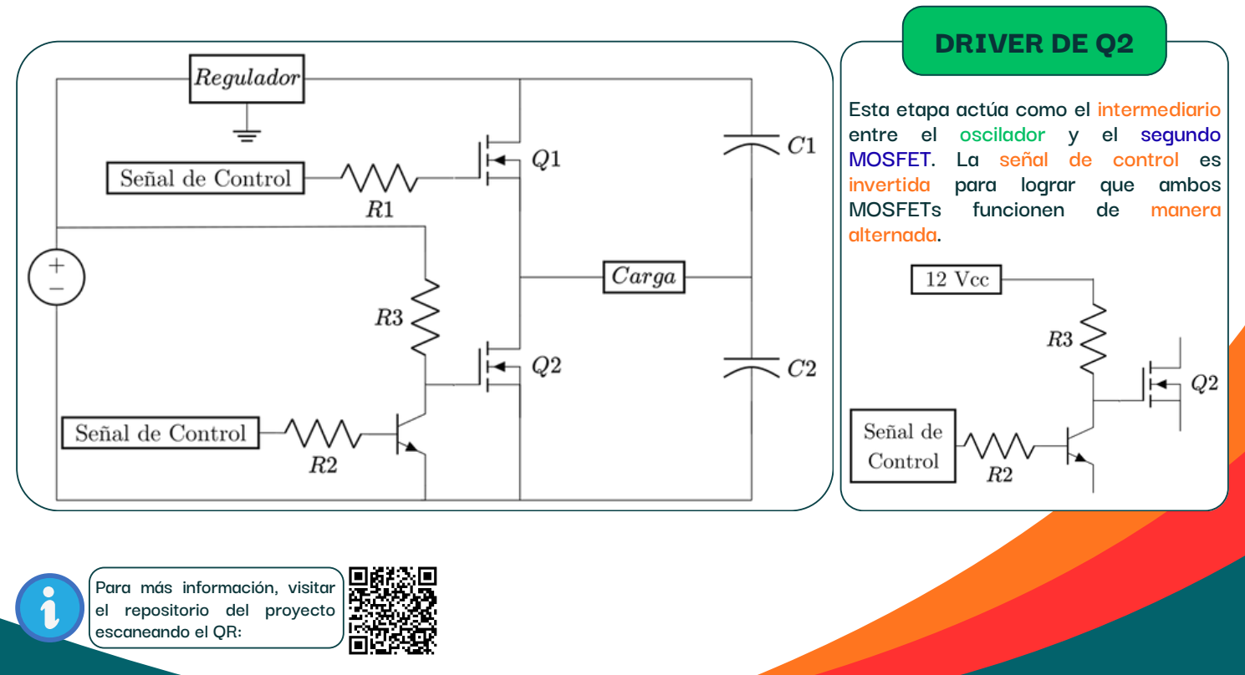
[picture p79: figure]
DRIVER DE Q2; Esta etapa actúa como el intermediario entre el oscilador y el segundo MOSFET. La señal de control es invertida para lograr que ambos MOSFETs funcionen de manera alternada.

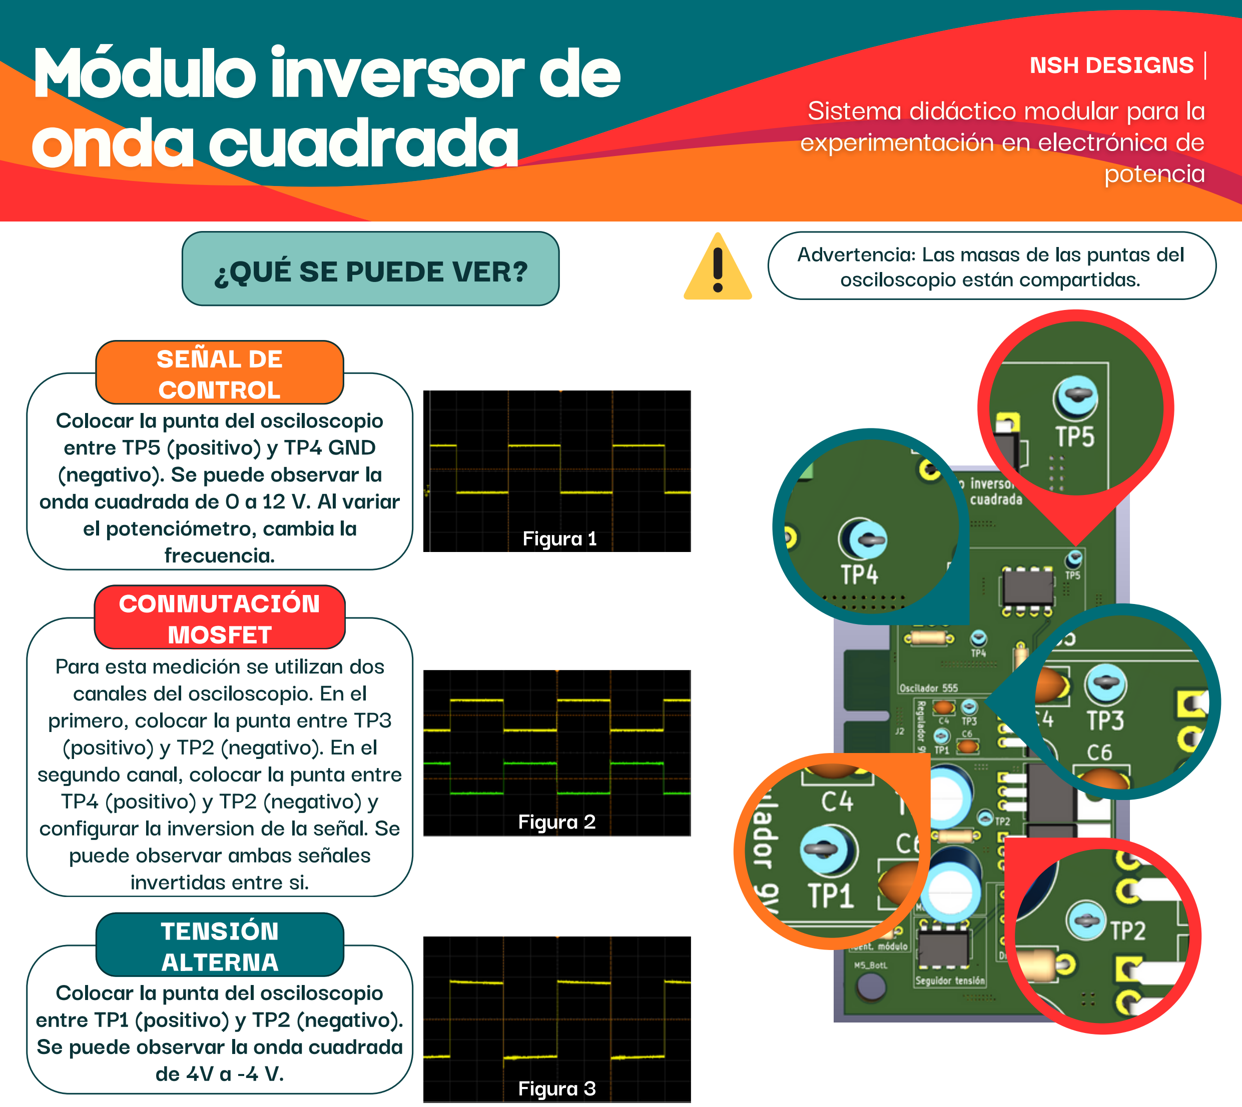
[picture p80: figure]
¿QUÉ SE PUEDE VER?; osciloscopio están compartidas.; TENSIÓN ALTERNA Colocar la punta del osciloscopio entre TP1 (positivo) y TP2 (negativo). Se puede observar la onda cuadrada de 4V a -4 V.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

Advertencia: Las masas de las puntas del

1.¿Qué tipo de señal genera el IC 555 en esta configuración?
2.¿Cómo influye el ajuste del potenciómetro en la frecuencia de la señal generada por el oscilador?
3.¿Qué relación existe entre la señal de control y la frecuencia de conmutación observada en los MOSFET?
4.¿Qué evidencia en el osciloscopio confirma que las señales de los MOSFETs están desfasadas 180°?
5.¿Qué efecto produciría variar la frecuencia del oscilador sobre la forma de onda alterna observada en TP1–TP2?
6.¿Qué diferencias se observarían si la carga fuera inductiva en lugar de resistiva? 7.¿Qué pasaría si ambos MOSFET condujeran al mismo tiempo?
8.¿Cómo se podría modificar el circuito para obtener una señal senoidal en lugar de cuadrada?

## PARA PENSAR

¿QUÉ ES? | ¿CÓMO FUNCIONA?
| Se basa en la utilización de un tiristor para recortar la onda de tensión aplicada a la carga, permitiendo así regular la potencia entregada. Al recortar la onda, se reduce la tensión RMS aplicada a la carga, lo que a su vez produce una reducción de potencia entregada.

## ¿QUÉ SE PUEDE MODIFICAR?

¡Este método de control de potencia es de baja eficiencia y de alta distorsión armónica! Su uso es limitado a cargas resistivas o cargas de baja sensibilidad a distorsiones, como lámparas y calentadores.

Un recortador de onda es uno de los métodos más simples para controlar la potencia entregada a una carga de corriente alterna.

Elección entre dos modos de control: Control analógico: se modifica una resistencia variable para variar el tiempo de carga de un capacitor, cambiando el punto de disparo del tiristor.
Control | digital: | mediante | un
microcontrolador, se modifica el tiempo de disparo luego del cruce por cero de la tensión de entrada.

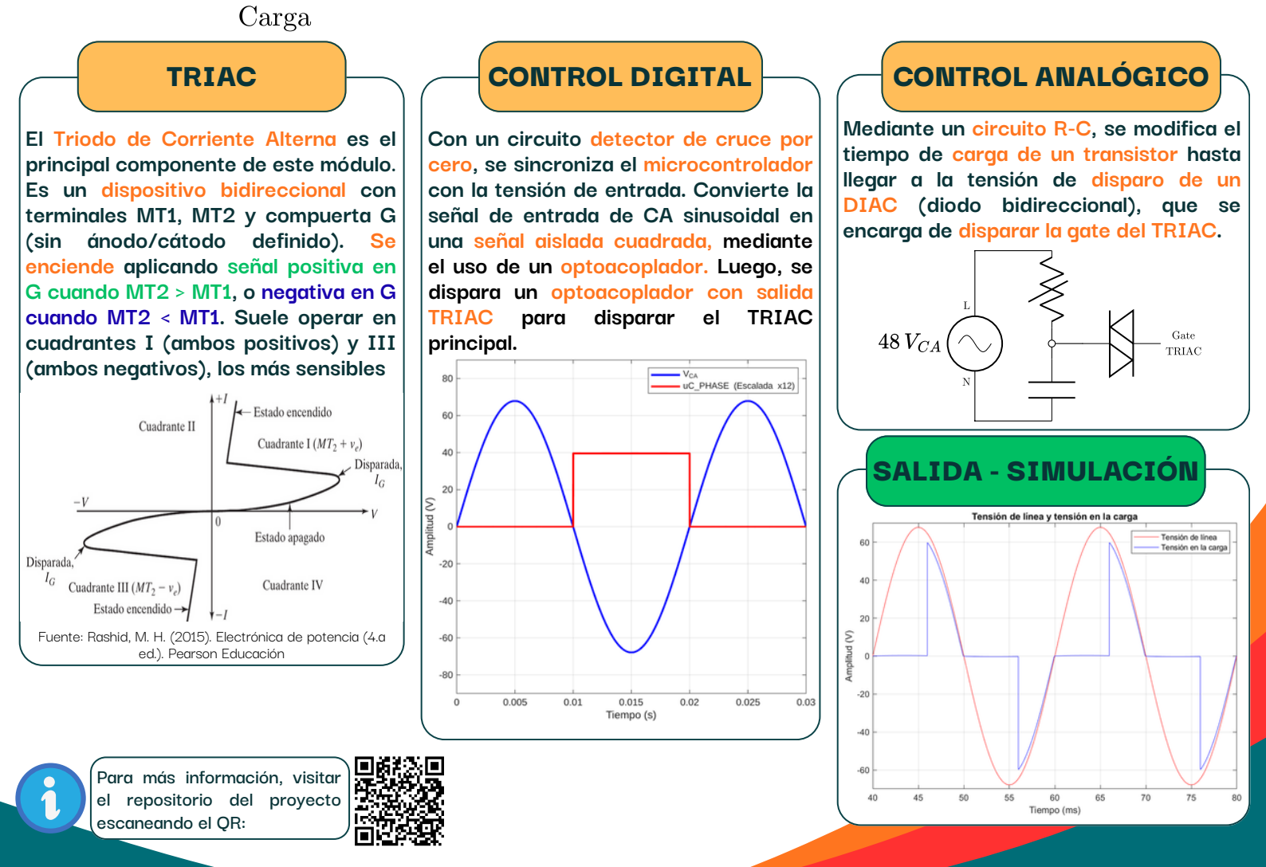
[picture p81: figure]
tiempo de carga de un transistor hasta llegar a la tensión de disparo de un DIAC (diodo bidireccional), que se encarga de disparar la gate del TRIAC.; SALIDA - SIMULACIÓN; CONTROL ANALÓGICO; Con un circuito detector de cruce por cero, se sincroniza el microcontrolador con la tensión de entrada. Convierte la señal de entrada de CA sinusoidal en una señal aislada cuadrada, mediante el uso de un optoacoplador. Luego, se dispara un optoacoplador con salida TRIAC para disparar el TRIAC principal.; CONTROL DIGITAL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

Mediante un circuito R-C, se modifica el

# Módulorecortador deonda

Fuente: Rashid, M. H. (2015). Electrónica de potencia (4.a

### potencia

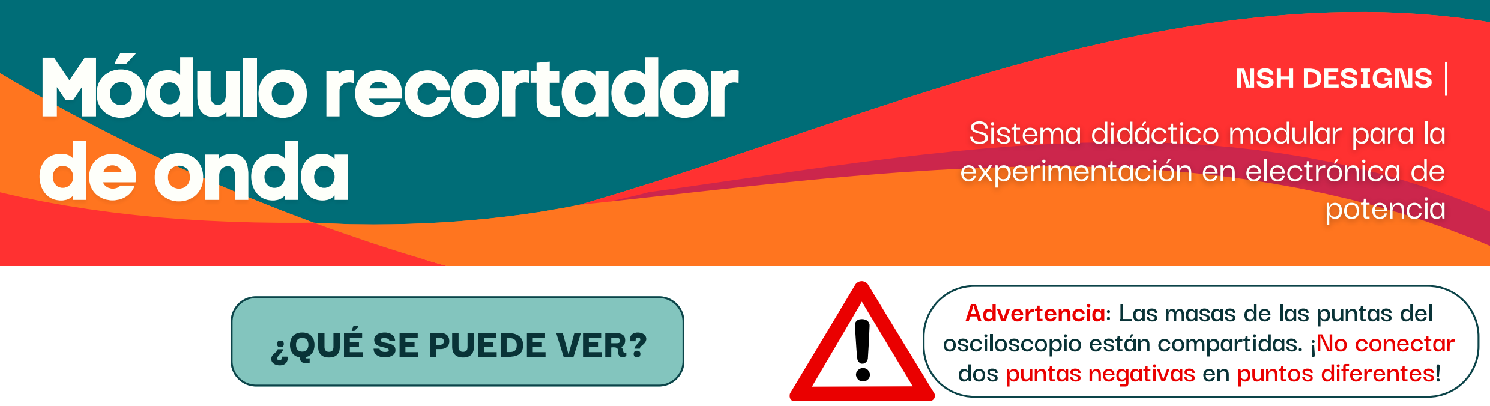
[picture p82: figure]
¿QUÉ SE PUEDE VER?; osciloscopio están compartidas. ¡No conectar; potencia; Módulorecortador deonda
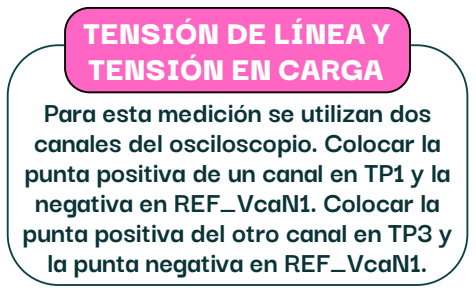
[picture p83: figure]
Para esta medición se utilizan dos canales del osciloscopio. Colocar la punta positiva de un canal en TP1 y la negativa en REF_VcaN1. Colocar la punta positiva del otro canal en TP3 y la punta negativa en REF_VcaN1.; TENSIÓN DE LÍNEA Y TENSIÓN EN CARGA
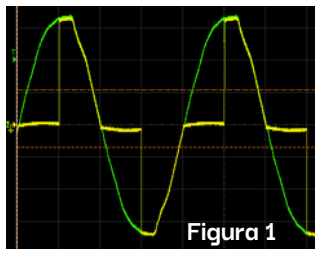
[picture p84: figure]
Figura 1

Advertencia: Las masas de las puntas del dos puntas negativas en puntos diferentes!

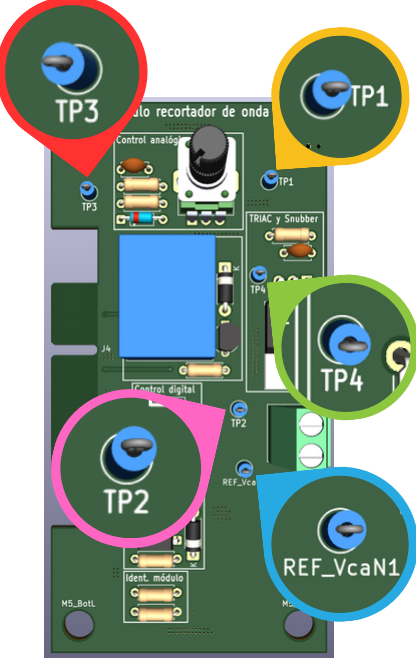
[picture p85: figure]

### TENSIÓN EN TERMINALES DE TRIAC

Figura 2
Figura 3
Figura 4

## PARA PENSAR

1.En modo analógico, ¿cuál es la forma de onda del capacitor cuando el potenciómetro está al mínimo (resistencia máxima)? ¿Por qué la forma de onda cambia a partir de un cierto valor de resistencia? ¿Qué cambia a medida que se reduce la resistencia?
2.En modo analógico, la carga (lámparas), ¿se encienden al mismo valor de potenciómetro al que se apagan? ¿Por qué?
3.En cualquier modo, en la gate del TRIAC, ¿a qué se debe el pulso períodico positivo y negativo? ¿Cuánto dura y qué significa esta duración? Luego de este pulso, ¿llega la tensión a cero? ¿Por qué?
4.En cualquier modo, ¿es lineal el cambio de tensión AC RMS en la carga respecto al cambio de tiempo de disparo? ¿A qué se debe?
5.En cualquier modo, ¿qué correlación tiene la tensión entre la MT2 y MT1 del TRIAC y la tensión en la carga?
6.Red Snubber: ¿por qué es importante la implementación de una red Snubber cuando se implementa un TRIAC?
7.Modos de control: ¿qué beneficios y desventajas tiene el modo de control digital sobre el analógico?

Colocar la punta positiva de un canal en TP3 y la negativa en TP2.

### TENSIÓN DE CAPACITOR

### TENSIÓN DE GATE DE TRIAC

Colocar la punta positiva de un canal en TP4 y la negativa en TP2.

Colocar la punta positiva de un canal en TP1 y la negativa en TP2.

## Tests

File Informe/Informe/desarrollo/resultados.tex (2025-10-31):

\vspace{-0.3cm}
\section{Resultados del proyecto}

El objetivo de esta sección es corroborar y justificar experimentalmente los cálculos y simulaciones realizadas en secciones anteriores, en los circuitos reales. Además, se muestran fotos del gabinete central y los gabinetes de los módulos desarrollados.
\vspace{-0.2cm}
\subsection{Gabinete central}

En la \cref{fig:resultados:gabinete_central}, se observan fotos del gabinete central. En la \cref{fig:resultados:gabinete_central_inside}, se observa, de izquierda a derecha, la PCB de control general, el transformador \SI{220}{\volt} - \SI{48}{\volt} y la fuente de alimentación de \SI{12}{\volt} de corriente continua.

\begin{figure}[H]
    \centering
    \begin{subfigure}[b]{0.49\textwidth} % Aumenté un poco el ancho para que sea más robusto
        \centering
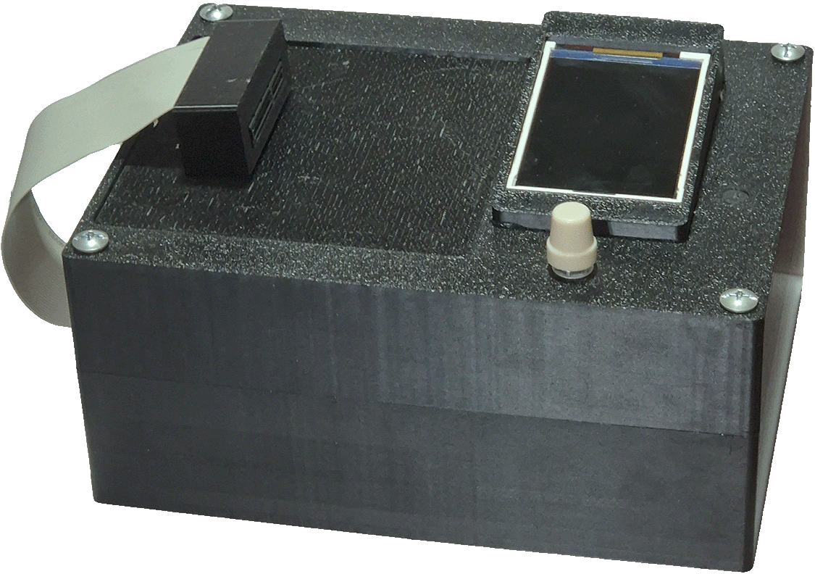
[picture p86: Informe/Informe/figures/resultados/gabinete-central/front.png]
        
        \caption{Vista frontal.}
        \label{fig:resultados:gabinete_central_front}
    \end{subfigure}
    \hfill 
    \begin{subfigure}[b]{0.49\textwidth}
        \centering
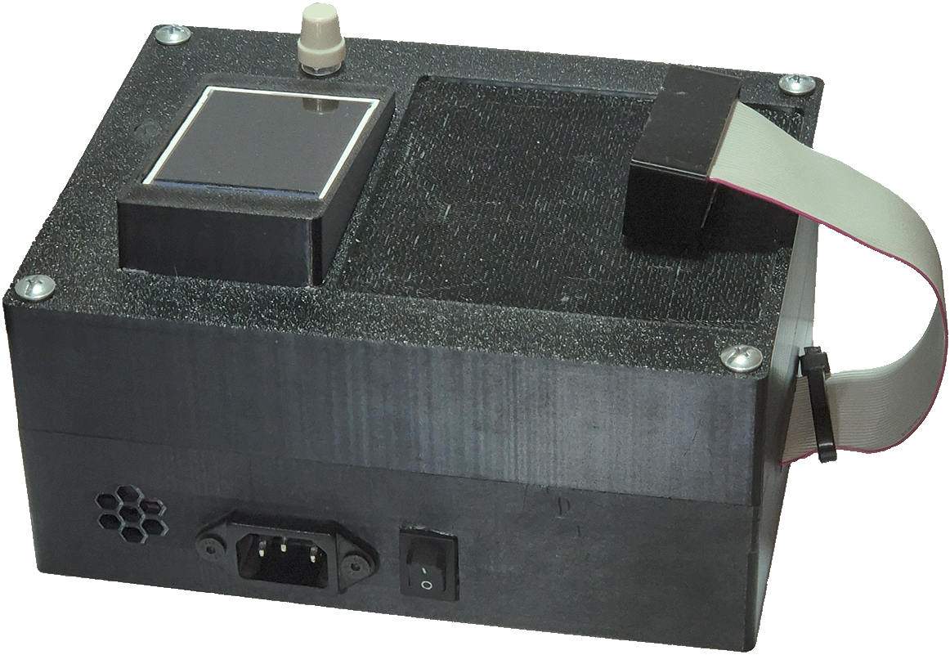
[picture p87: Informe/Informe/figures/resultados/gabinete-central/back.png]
        
        \caption{Vista trasera.}
        \label{fig:resultados:gabinete_central_back}
    \end{subfigure}
  
    \begin{subfigure}[b]{\columnwidth}
        \centering
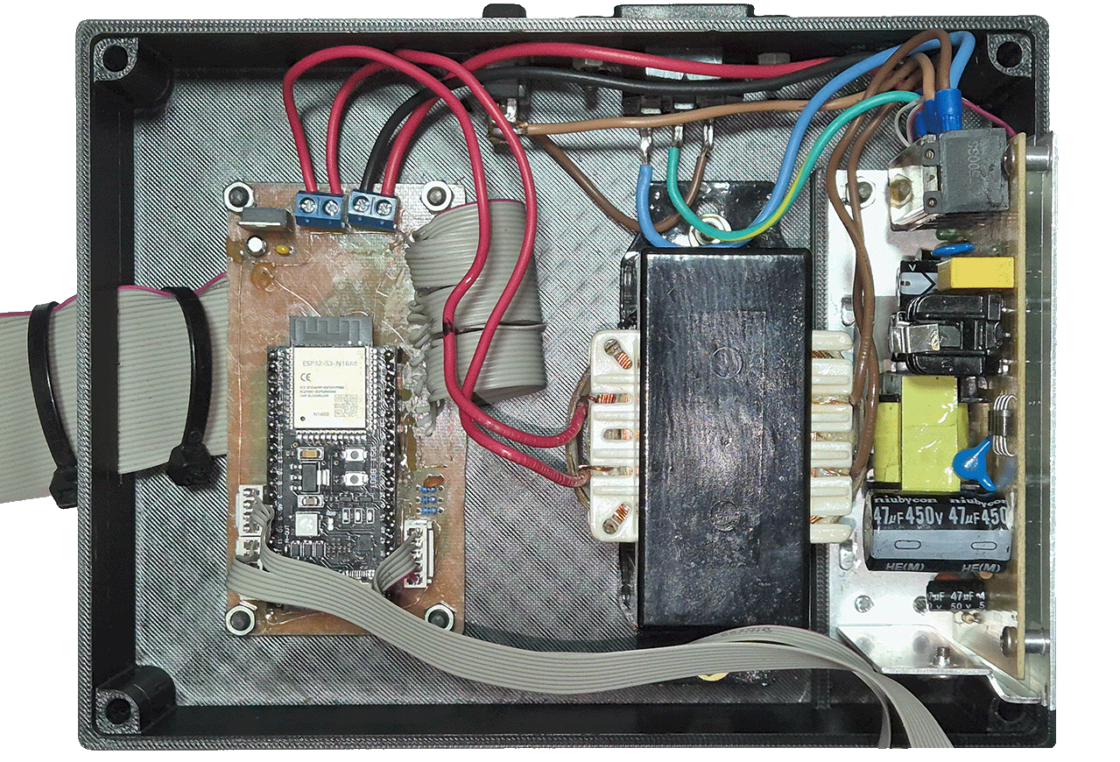
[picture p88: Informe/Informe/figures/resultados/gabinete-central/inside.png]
        
        \caption{Interior del gabinete.}
        \label{fig:resultados:gabinete_central_inside}
    \end{subfigure}
    \caption{Gabinete central del sistema.}
    \label{fig:resultados:gabinete_central}
\end{figure}

\subsection{Módulo convertidor reductor o Buck}

Se presentan los resultados experimentales obtenidos con el convertidor reductor o Buck, en las pruebas realizadas en el laboratorio, por medio del uso de osciloscopio y multímetro. 

\begin{figure}[H]
    \centering
    
    \caption{Gabinete del módulo convertidor reductor.}
    \label{fig:resultados:buck:gabinete}
\end{figure}

Los datos experimentales obtenidos son para una tensión de salida de \SI{6}{\volt} con una corriente de \SI{1.2}{\ampere}, siendo una potencia teórica de \SI{7.2}{\watt}, la carga elegida para las pruebas es la resistiva, y no se presenta ningún control, se trabaja en lazo abierto.

%\paragraph{Tensión de salida pre-filtrado}
En la \cref{fig:resultados:buck:tension-gate-mosfet}, la tensión $V_{g}$ (IRF9540) es una señal cuadrada de \SI{12}{\volt} de amplitud, con un \textit{duty cycle} del \SI{44}{\percent}. Esta señal es opuesta a la forma del PWM enviado por el microcontrolador, ya que en el momento que el \textit{driver} BJT conduce, la tensión en la \textit{gate} es \SI{0}{\volt} haciendo que el transistor de conmutación de potencia conduzca, debido a una $V_{gs}$ negativa. Ocurre lo contrario cuando el driver no conduce, ya que la tensión $V_g$ es de \SI{12}{\volt}, quedando una $V_{gs} \approx \SI{0}{\volt}$.

La \cref{fig:resultados:buck:tension-drenador} muestra una señal que sigue la forma de la señal PWM entregada por el microcontrolador. Esta señal representa la tensión de salida previa a la etapa de filtrado.

\begin{figure}[H]
    \centering
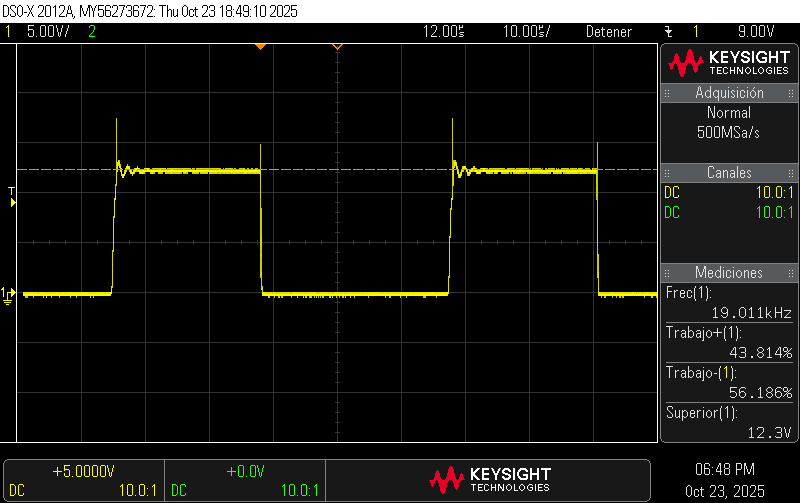
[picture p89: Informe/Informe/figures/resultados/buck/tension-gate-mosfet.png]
    
    \caption{Tensión de \textit{gate} del transistor IRF9540.}
    \label{fig:resultados:buck:tension-gate-mosfet}
\end{figure}

\begin{figure}[H]
    \centering
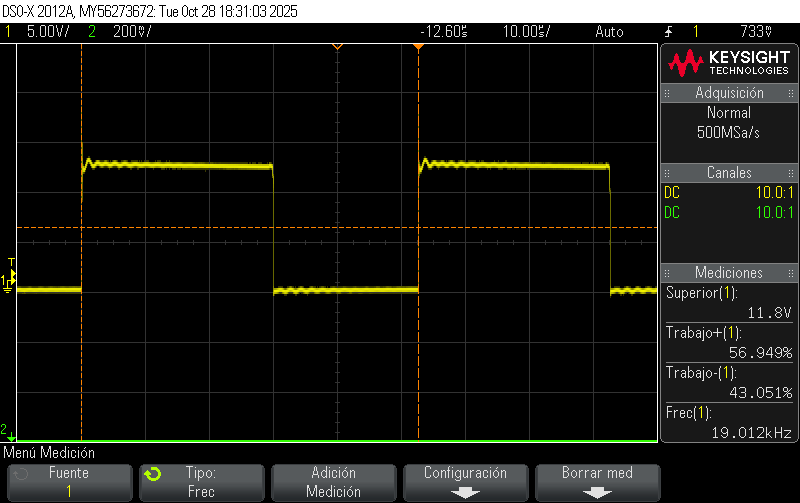
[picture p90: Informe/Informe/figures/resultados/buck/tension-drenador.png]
    
    \caption{Tensión conmutada en drenador del transistor IRF9540.}
    \label{fig:resultados:buck:tension-drenador}
\end{figure}

En la \cref{fig:resultados:buck:tensiones-salida-buck} se muestran las tensiones de salida del convertidor frente a dos cargas distintas, una inductiva (\cref{fig:resultados:buck:tension-salida-inductiva}) y otra resistiva (\cref{fig:resultados:buck:tension-salida-resistiva}). La tensión resistiva respeta la tensión de salida calculada para un valor de \textit{duty cycle} de \SI{55}{\percent}, mientras que la inductiva no lo hace, ya que su naturaleza (reactiva/activa) impide que se cumpla la relación ideal, $V_{out} = V_{in} \, D$ (D, \textit{duty cycle}), válida únicamente para cargas pasivas en modo de conducción continua, \parencite{DANIEL-HART-SPANISH}.

\begin{figure}[H]
    \centering
    \begin{subfigure}[b]{0.49\textwidth}
        \centering
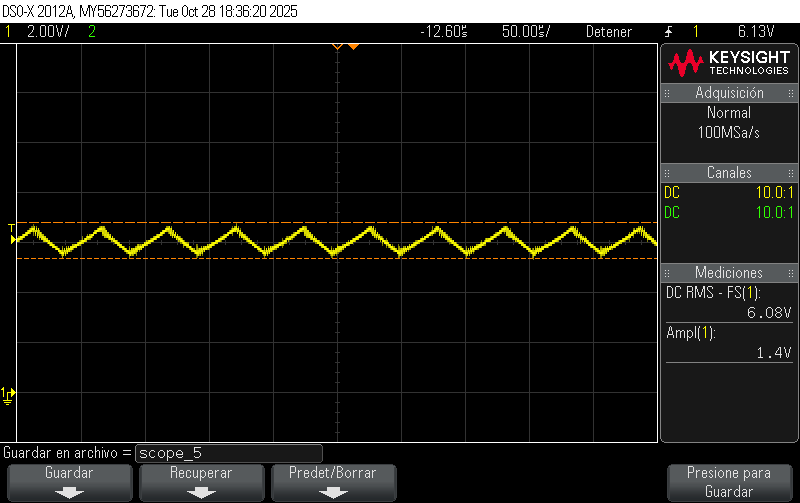
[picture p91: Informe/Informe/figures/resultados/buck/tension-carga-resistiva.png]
        
        \caption{Carga resistiva.}
        \label{fig:resultados:buck:tension-salida-resistiva}
    \end{subfigure}
    \hfill
    \begin{subfigure}[b]{0.49\textwidth} 
        \centering
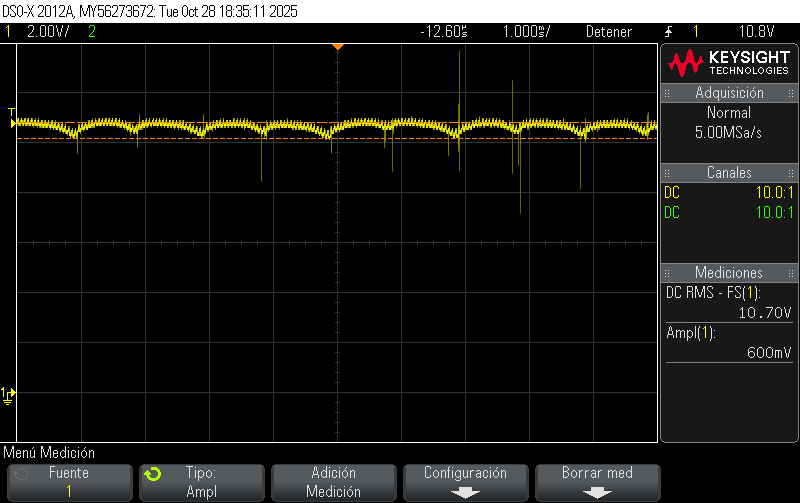
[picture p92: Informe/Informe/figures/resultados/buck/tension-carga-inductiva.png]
        
        \caption{Carga inductiva.}
        \label{fig:resultados:buck:tension-salida-inductiva}
    \end{subfigure}
    \caption{Tensión de salida del convertidor con \textit{duty cycle} de \SI{55}{\percent}, según tipo de carga.}
    \label{fig:resultados:buck:tensiones-salida-buck}
\end{figure}

Cuando la carga es resistiva, la tensión de salida responde linealmente al PWM entregado por el microcontrolador, como se observa en la \cref{fig:resultados:buck:pwm-carga-resistiva}. Mientras que, con la carga inductiva, el PWM entregado por el microcontrolador no afecta de manera lineal a la tensión de salida, \cref{fig:resultados:buck:pwm-carga-inductiva}.

\begin{figure}[H]
    \centering
    \begin{subfigure}[b]{0.49\textwidth} 
        \centering
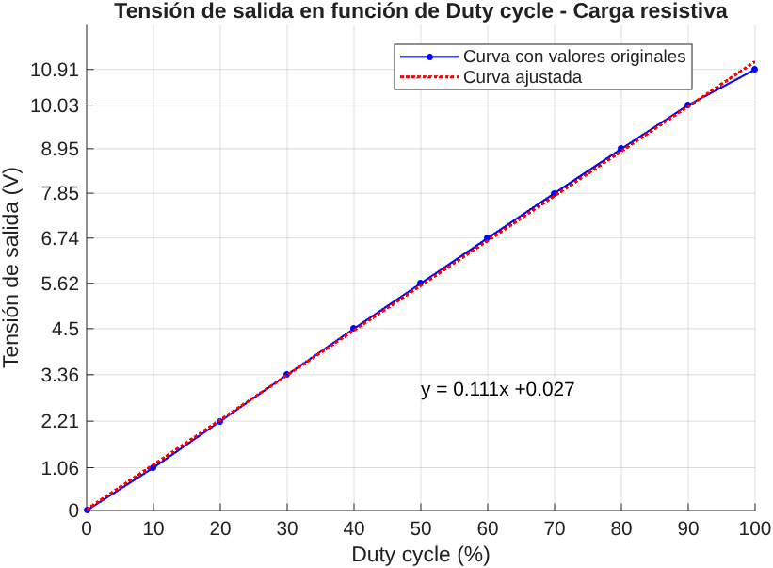
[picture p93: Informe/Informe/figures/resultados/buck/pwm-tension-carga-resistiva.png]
        
        \caption{Carga resistiva.}
        \label{fig:resultados:buck:pwm-carga-resistiva}
    \end{subfigure}
    \hfill 
    \begin{subfigure}[b]{0.49\textwidth}
        \centering
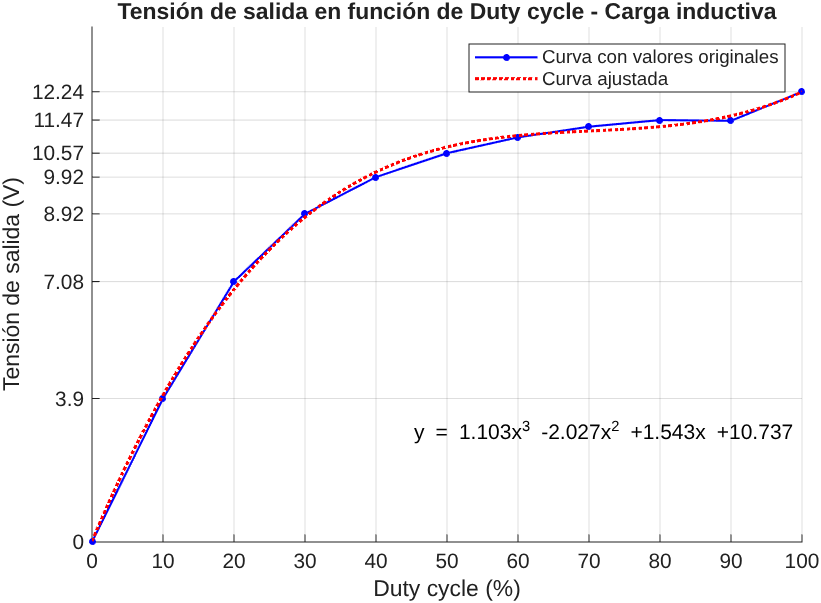
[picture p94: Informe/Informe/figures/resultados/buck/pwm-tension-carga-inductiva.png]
        
        \caption{Carga inductiva.}
        \label{fig:resultados:buck:pwm-carga-inductiva}
    \end{subfigure}
    \caption{Tensión de salida del convertidor en función del PWM entregado por el microcontrolador, según tipo de carga.}
    \label{fig:resultados:buck:pwm-vs-tension-salida}
\end{figure}

Como prueba adicional, se realizan las mediciones de corriente tanto en el inductor como en el capacitor, \cref{fig:resultados:buck:formas-onda-corriente}. En la \cref{fig:resultados:buck:corriente-inductor} se muestra la corriente a través del inductor, siendo la corriente teórica de  \SI{1.2}{\ampere}. Como el amplificador operacional utilizado entrega una tensión, se realiza una conversión para obtener la corriente, \cref{eq:resultados:buck:corriente-inductor}. Esta ecuación se despeja de las \cref{eq:buck:salida_amplificador_unidireccional,eq:buck:resistencia_shunt_unidireccional} del \cref{sec:buck:medicion_corriente}.

\begin{equation} \label{eq:resultados:buck:corriente-inductor}
    I_{inductor} = \frac{V_{out}}{R_{shunt}\,ganancia}
\end{equation}

El cálculo con el valor experimental mostrado en la \cref{fig:resultados:buck:corriente-inductor} resulta en una corriente de \SI{1.27}{\ampere}.
El valor de tensión necesario es el valor medio de tensión de la señal mostrada en la figura, obtenido a través de la \cref{eq:resultados:buck:tension-media-para-corriente}.

\begin{equation} \label{eq:resultados:buck:tension-media-para-corriente}
    V_{out(med)} = \frac{V_{max}+V_{min}}{2} = \frac{V_{max}+(V_{max}-V_{p-p})}{2}
\end{equation}

\begin{figure}[H]
    \centering
    \begin{subfigure}[b]{0.49\textwidth} 
        \centering
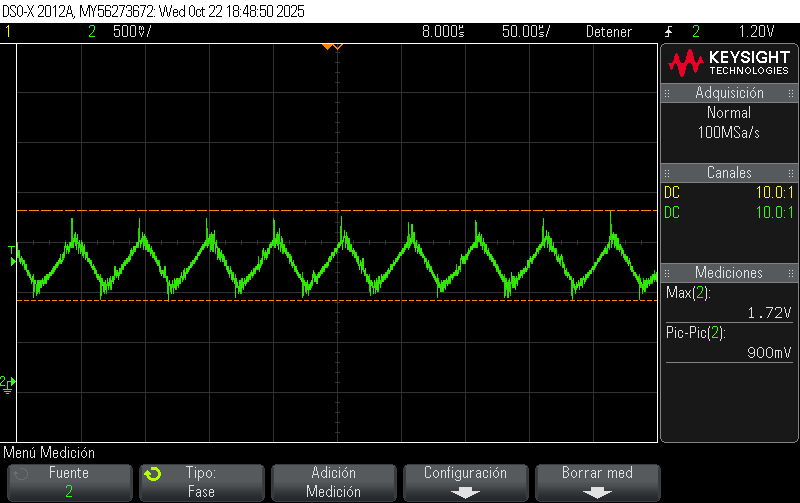
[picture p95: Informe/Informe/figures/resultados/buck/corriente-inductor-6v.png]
        
        \caption{Inductor.}
        \label{fig:resultados:buck:corriente-inductor}
    \end{subfigure}
    \hfill 
    \begin{subfigure}[b]{0.49\textwidth}
        \centering
        
        \caption{Capacitor.}
        \label{fig:resultados:buck:corriente-capacitor}
    \end{subfigure}
    \caption{Formas de onda de corriente.}
    \label{fig:resultados:buck:formas-onda-corriente}
\end{figure}

Para calcular el valor real del capacitor se aplica la \cref{eq:resultados:buck:corriente-capacitor}.

\begin{equation} \label{eq:resultados:buck:corriente-capacitor}
    I_{capacitor} = \frac{V_{out}-V_{ref}}{R_{shunt} \, ganancia}
\end{equation}

Otra prueba posible es demostrar los distintos modos de conducción del convertidor. Se puede visualizar la forma de onda de la corriente en el inductor mientras se varía el \textit{duty cycle}, manteniendo la carga constante.

Se observa que, con un \textit{duty cycle} de un \SI{55}{\percent}, el convertidor opera en modo de conducción continua (CCM), donde la corriente a través del inductor no llega a cero. A medida que se disminuye el \textit{duty cycle} (a \SI{8}{\percent} aproximadamente), la corriente media en la carga disminuye, provocando que la corriente mínima en el inductor descienda hasta que se vuelve nula durante una porción del ciclo, entrando así en modo de conducción discontinua (DCM).

Para facilitar la observación de este fenómeno, el ensayo se configura con una frecuencia de conmutación de \SI{3}{\kilo\hertz}, con el fin de incrementar la magnitud del \textit{ripple} de corriente en relación a la corriente media, permitiendo que la transición entre los distintos modos de conducción sea más evidente.

En la \cref{fig:resultados:buck:modo-conduccion-ccm-dcm}, se muestran los resultados, donde la \cref{fig:resultados:buck:corriente-inductor-ccm} representa al convertidor funcionando en modo de conducción continua, ya que la corriente en el inductor no alcanza la corriente nula. En cambio, en la \cref{fig:resultados:buck:corriente-inductor-dcm}, se aprecia que para valores bajos de \textit{duty cycle} (entre \SIrange{5}{10}{\percent}), la corriente en el inductor es nula.

\begin{figure}[H]
    \centering
    \begin{subfigure}[b]{0.49\textwidth} 
        \centering
        
        \caption{Modo de conducción continua (CCM).}
        \label{fig:resultados:buck:corriente-inductor-ccm}
    \end{subfigure}
    \hfill 
    \begin{subfigure}[b]{0.49\textwidth}
        \centering
        
        \caption{Modo de conducción discontinua (DCM).}
        \label{fig:resultados:buck:corriente-inductor-dcm}
    \end{subfigure}
    \caption{Corriente en el inductor en distintos modos de conducción.}
    \label{fig:resultados:buck:modo-conduccion-ccm-dcm}
\end{figure}

%----------------------------------%

\subsection{Módulo recortador de onda}

Se presentan los resultados experimentales obtenidos con el recortador de onda, en las pruebas realizadas en el laboratorio, por medio del uso de osciloscopio y multímetro. 

\begin{figure}[H]
    \centering
    
    \caption{Gabinete del módulo recortador de onda.}
    \label{fig:resultados:dimmer:gabinete}
\end{figure}

En la \cref{fig:resultados:dimmer:linea_carga}, se puede observar el correcto funcionamiento del circuito de control analógico, recortando la onda de entrada y aplicando a la carga una tensión de valor RMS menor y, por lo tanto, menor potencia.

\begin{figure}[H]
    \centering
    
    \caption{Recortador de onda en control analógico. Señal verde: tensión de entrada. Señal amarilla: tensión aplicada en la carga }
    \label{fig:resultados:dimmer:linea_carga}
\end{figure}

En la \cref{fig:resultados:dimmer:analogico}, se observa la carga y descarga del capacitor de la rama R-C según distintos valores de resistencia en serie. Cuando la resistencia es máxima, la tensión en el capacitor es sinusoidal, ya que en ningún momento alcanza la tensión de disparo del DIAC (\SI{32}{\volt}). Una vez que la resistencia disminuye, la forma de onda cambia a una de carga y descarga, reduciendo el tiempo de disparo a medida que se reduce la resistencia. El potenciómetro se encuentra configurado para reducir la resistencia a medida que se gira en sentido horario. De esta forma, el usuario aumenta la potencia entregada a la carga girando el potenciómetro en sentido horario, y reduce la potencia entregada a la carga girando el potenciómetro en sentido antihorario.

\begin{figure}[H]
    \centering
    \begin{subfigure}[b]{0.49\textwidth} % Aumenté un poco el ancho para que sea más robusto
        \centering
        
        \caption{Potenciómetro al mínimo (resistencia máxima).}
        \label{fig:resultados:dimmer:analogico0}
    \end{subfigure}
    \hfill 
    \begin{subfigure}[b]{0.49\textwidth}
        \centering
        
        \caption{Potenciómetro en la mitad (resistencia media).}
        \label{fig:resultados:dimmer:analogico50}
    \end{subfigure}
  
    \begin{subfigure}[b]{\columnwidth}
        \centering
        
        \caption{Potenciómetro al máximo (resistencia mínima).}
        \label{fig:resultados:dimmer:analogico100}
    \end{subfigure}
    \caption{Recortador de onda funcionando en modo analógico. Señal verde: tensión de capacitor de rama R-C. Señal amarilla: tensión aplicada en la carga.}
    \label{fig:resultados:dimmer:analogico}
\end{figure}

En la \cref{fig:resultados:dimmer:vgate}, se observa el comportamiento de la tensión en la \textit{gate} del TRIAC. Se observa que, cuando se dispara, se produce un pico de tensión, un pulso de aproximadamente \SI{2}{\micro\second}, que corresponde con tiempo de encendido del TRIAC controlado por la \textit{gate}, \parencite{BT137}. Luego, la tensión no disminuye a cero, sino a una menor a \SI{1}{\volt}, necesaria para suministrar a la \textit{gate} la corriente de mantenimiento del TRIAC (\SIrange{2.5}{20}{\milli\ampere}), \parencite{BT137}.

\begin{figure}[H]
    \centering
    \begin{subfigure}[b]{0.49\textwidth}
        \centering
        
        \caption{Carga resistiva.}
        \label{fig:resultados:dimmer:vgate_vload}
    \end{subfigure}
    \hfill
    \begin{subfigure}[b]{0.49\textwidth} 
        \centering
        
        \caption{Vista ampliada del pulso en la tensión de \textit{gate} del TRIAC.}
        \label{fig:resultados:dimmer:vgate_pulse}
    \end{subfigure}
    \caption{Recortador de onda funcionando en modo analógico. Señal verde: tensión de gate del TRIAC. Señal amarilla: tensión aplicada en la carga.}
    \label{fig:resultados:dimmer:vgate}
\end{figure}

En la \cref{fig:resultados:dimmer:digital}, se observa el funcionamiento del circuito en modo digital. Se visualiza el recorte de la onda según cuándo se aplica tensión en la \textit{gate} del TRIAC, que ocurre cuando el microcontrolador envía un pulso al optoacoplador con salida TRIAC, que aplica la tensión de línea a la \textit{gate}.

\begin{figure}[H]
    \centering
    \begin{subfigure}[b]{0.49\textwidth} % Aumenté un poco el ancho para que sea más robusto
        \centering
        
        \caption{Tiempo de espera máximo (\SI{9.2}{\milli\second}).}
        \label{fig:resultados:dimmer:digital0}
    \end{subfigure}
    \hfill 
    \begin{subfigure}[b]{0.49\textwidth}
        \centering
        
        \caption{Tiempo de espera medio (\SI{5}{\milli\second}).}
        \label{fig:resultados:dimmer:digital50}
    \end{subfigure}
  
    \begin{subfigure}[b]{\columnwidth}
        \centering
        
        \caption{Tiempo de espera mínimo (\SI{1}{\milli\second}).}
        \label{fig:resultados:dimmer:digital100}
    \end{subfigure}
    \caption{Recortador de onda funcionando en modo digital. Señal verde: tensión de \textit{gate} en TRIAC. Señal amarilla: tensión aplicada en la carga.}
    \label{fig:resultados:dimmer:digital}
\end{figure}

%----------------------------------%

\subsection{Módulo inversor de onda cuadrada}

Se presentan los resultados experimentales obtenidos con el inversor de onda cuadrada, en las pruebas realizadas en el laboratorio, por medio del uso de osciloscopio y multímetro. 

\begin{figure}[H]
    \centering
    
    \caption{Gabinete del módulo inversor de onda cuadrada.}
    \label{fig:resultados:inversor:gabinete}
\end{figure}

%\paragraph{Señal de control}
En la \cref{fig:resultados:inversor:inversor_555_50hz} se muestra la señal cuadrada de salida del IC 555, con una frecuencia de \SI{50}{\hertz} y un \textit{duty cycle} del \SI{50}{\percent}, que es utilizada para controlar el medio puente del inversor. Al variar el potenciómetro, varía la frecuencia de la señal, sin modificar significativamente el \textit{duty cycle}; por ejemplo al cambiar a \SI{60}{\hertz}, como se observa en la \cref{fig:resultados:inversor:inversor_555_60hz}.

\begin{figure}[H]
    \centering
    \begin{subfigure}[b]{0.49\textwidth} 
        \centering
        
        \caption{50 Hz.}
        \label{fig:resultados:inversor:inversor_555_50hz}
    \end{subfigure}
    \hfill 
    \begin{subfigure}[b]{0.49\textwidth}
        \centering
        
        \caption{60 Hz.}
        \label{fig:resultados:inversor:inversor_555_60hz}
    \end{subfigure}
    \caption{Señal de control.}
    \label{fig:resultados:inversor:senal-control-inversor}
\end{figure}

%\paragraph{Señal alternada en MOSFETs}
En la \cref{fig:resultados:inversor:inversor_mosfet_ds} se muestra la tensión drenador-surtidor de los MOSFETs que conforman el medio puente, donde se observa que una es la inversa de la otra. Esto significa que, cuando uno de los MOSFETs está conduciendo, el otro está apagado y viceversa, generando así la señal alterna.

\begin{figure}[H]
    \centering
    
    \caption{Tensión drenador-surtidor de los MOSFETs. En amarillo, Q1 y en verde, Q2.}
    \label{fig:resultados:inversor:inversor_mosfet_ds}
\end{figure}

%\paragraph{Tensión alterna}
En la \cref{fig:resultados:inversor:carga-alterna} se muestra la tensión aplicada a la carga, en dos frecuencias distintas, \SI{50}{\hertz} (\cref{fig:resultados:inversor:inversor_carga_50hz}) y \SI{60}{\hertz} (\cref{fig:resultados:inversor:inversor_carga_60hz}). La tensión alterna RMS de salida es de aproximadamente \SI{3.6}{\volt} en ambos casos, con una carga resistiva de \SI{100}{\ohm}.

\begin{figure}[H]
    \centering
    \begin{subfigure}[b]{0.49\textwidth} 
        \centering
        
        \caption{50 Hz.}
        \label{fig:resultados:inversor:inversor_carga_50hz}
    \end{subfigure}
    \hfill 
    \begin{subfigure}[b]{0.49\textwidth}
        \centering
        
        \caption{60 Hz.}
        \label{fig:resultados:inversor:inversor_carga_60hz}
    \end{subfigure}
    \caption{Tensión alterna.}
    \label{fig:resultados:inversor:carga-alterna}
\end{figure}

\subsection{Manuales de usuario}

En el Anexo, \cref{sec:apendice}, se presentan los manuales de usuario desarrollados para cada módulo. Cada uno contiene una explicación sintetizada de qué es, cómo funciona, su composición, las señales a visualizar y preguntas para pensar.

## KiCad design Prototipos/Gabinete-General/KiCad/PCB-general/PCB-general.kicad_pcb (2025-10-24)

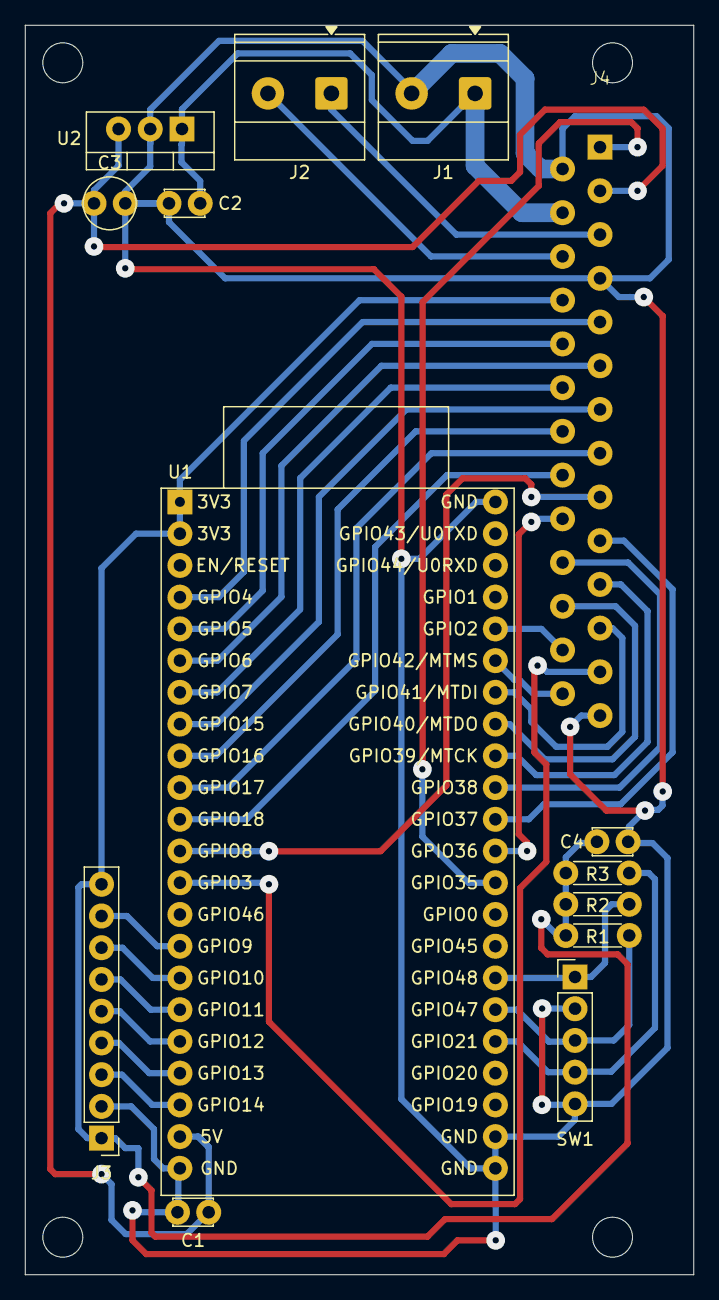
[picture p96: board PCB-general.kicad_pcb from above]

Board: 2 copper layers, 53.5 x 100.0 mm, 18 parts (0 on the bottom side), 34 nets.

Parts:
C1, C2: 330 nF; C_Disc_D3.0mm_W2.0mm_P2.50mm
C3: 1uF; C_Radial_D4.0mm_H7.0mm_P1.50mm
C4: 100 nF; C_Disc_D3.0mm_W2.0mm_P2.50mm
J1, J2: Conn_01x02; TerminalBlock_Phoenix_MKDS-1,5-2-5.08_1x02_P5.08mm_Horizont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
J3: TFT Display; PinHeader_1x09_P2.54mm_Vertical
J4: PCIe X4; PCIE_x4_Gabinete_NSH
M3_BL, M3_BR, M3_TL, M3_TR: MountingHole_3.2mm_M3
R1, R2, R3: 10k; R_Axial_DIN0204_L3.6mm_D1.6mm_P5.08mm_Horizontal
SW1: RotaryEncoder_Switch; PinHeader_1x05_P2.54mm_Vertical
U1: ESP32-S3-DevKitC; ESP32-S3-DevKitC_NSH
U2: LM7805_TO220; TO-220-3_Vertical

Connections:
3.3Vdc: C4.2, J3.1 (Vcc), J3.9 (LED), J4.8 (3,3Vdc_Signal), R1.1, R2.1, R3.1, U1.1 (3V3), U1.2 (3V3)
5Vdc: C1.1, C3.1, J4.3 (5Vdc), U1.21 (5V), U2.3 (VO)
12Vdc: C2.1, J1.1, J4.4 (12Vdc), U2.1 (VI)
48Vac_L: J2.1, J4.5 (48Vac_L)
48Vac_N: J2.2, J4.6 (48Vac_N)
GND: C1.2, C2.2, C3.2, C4.1, J1.2, J3.2 (GND), J4.2 (PGND), J4.7 (AGND), SW1.2, SW1.5, U1.22 (GND), U1.23 (GND), U1.24 (GND), U1.44 (GND), U2.2 (GND)
PCIe_HP_Power: J4.1 (HP_Power), U1.32 (GPIO35)
PCIe_HP_Signal: J4.26 (HP_Signal), U1.39 (GPIO42/MTMS)
PCIe_MODULE_IDENT: J4.25 (MODULE_IDENT), U1.13 (GPIO3/ADC1_CH2)
PCIe_S1: J4.9 (S1), U1.4 (GPIO4/ADC1_CH3)
PCIe_S2: J4.10 (S2), U1.5 (GPIO5/ADC1_CH4)
PCIe_S3: J4.11 (S3), U1.6 (GPIO6/ADC1_CH5)
PCIe_S4: J4.12 (S4), U1.7 (GPIO7/ADC1_CH6)
PCIe_S5: J4.13 (S5), U1.8 (GPIO15/ADC2_CH4/32K_P)
PCIe_S6: J4.14 (S6), U1.9 (GPIO16/ADC2_CH5/32K_N)
PCIe_S7: J4.15 (S7), U1.10 (GPIO17/ADC2_CH6)
PCIe_S8: J4.16 (S8), U1.11 (GPIO18/ADC2_CH7)
PCIe_S9: J4.17 (S9), U1.12 (GPIO8/ADC1_CH7)
PCIe_S10: J4.18 (S10), U1.33 (GPIO36)
PCIe_S11: J4.19 (S11), U1.34 (GPIO37)
PCIe_S12: J4.20 (S12), U1.35 (GPIO38)
PCIe_S13: J4.21 (S13), U1.36 (GPIO39/MTCK)
PCIe_S14: J4.22 (S14), U1.37 (GPIO40/MTDO)
PCIe_S15: J4.23 (S15), U1.38 (GPIO41/MTDI)
PCIe_S16: J4.24 (S16), U1.40 (GPIO2/ADC1_CH1)
ROTARY_CLK: R2.2, SW1.1, U1.29 (GPIO48)
ROTARY_DATA: R1.2, SW1.3, U1.28 (GPIO47)
ROTARY_SW: R3.2, SW1.4, U1.27 (GPIO21)
TFT_CS: J3.3 (CS), U1.20 (GPIO14/ADC2_CH3)
TFT_DC: J3.5 (DC), U1.18 (GPIO12/ADC2_CH1)
TFT_MISO: J3.8 (MISO), U1.15 (GPIO9/ADC1_CH8)
TFT_MOSI: J3.6 (MOSI), U1.17 (GPIO11/ADC2_CH0)
TFT_RESET: J3.4 (RESET), U1.19 (GPIO13/ADC2_CH2)
TFT_SCK: J3.7 (SCK), U1.16 (GPIO10/ADC1_CH9)

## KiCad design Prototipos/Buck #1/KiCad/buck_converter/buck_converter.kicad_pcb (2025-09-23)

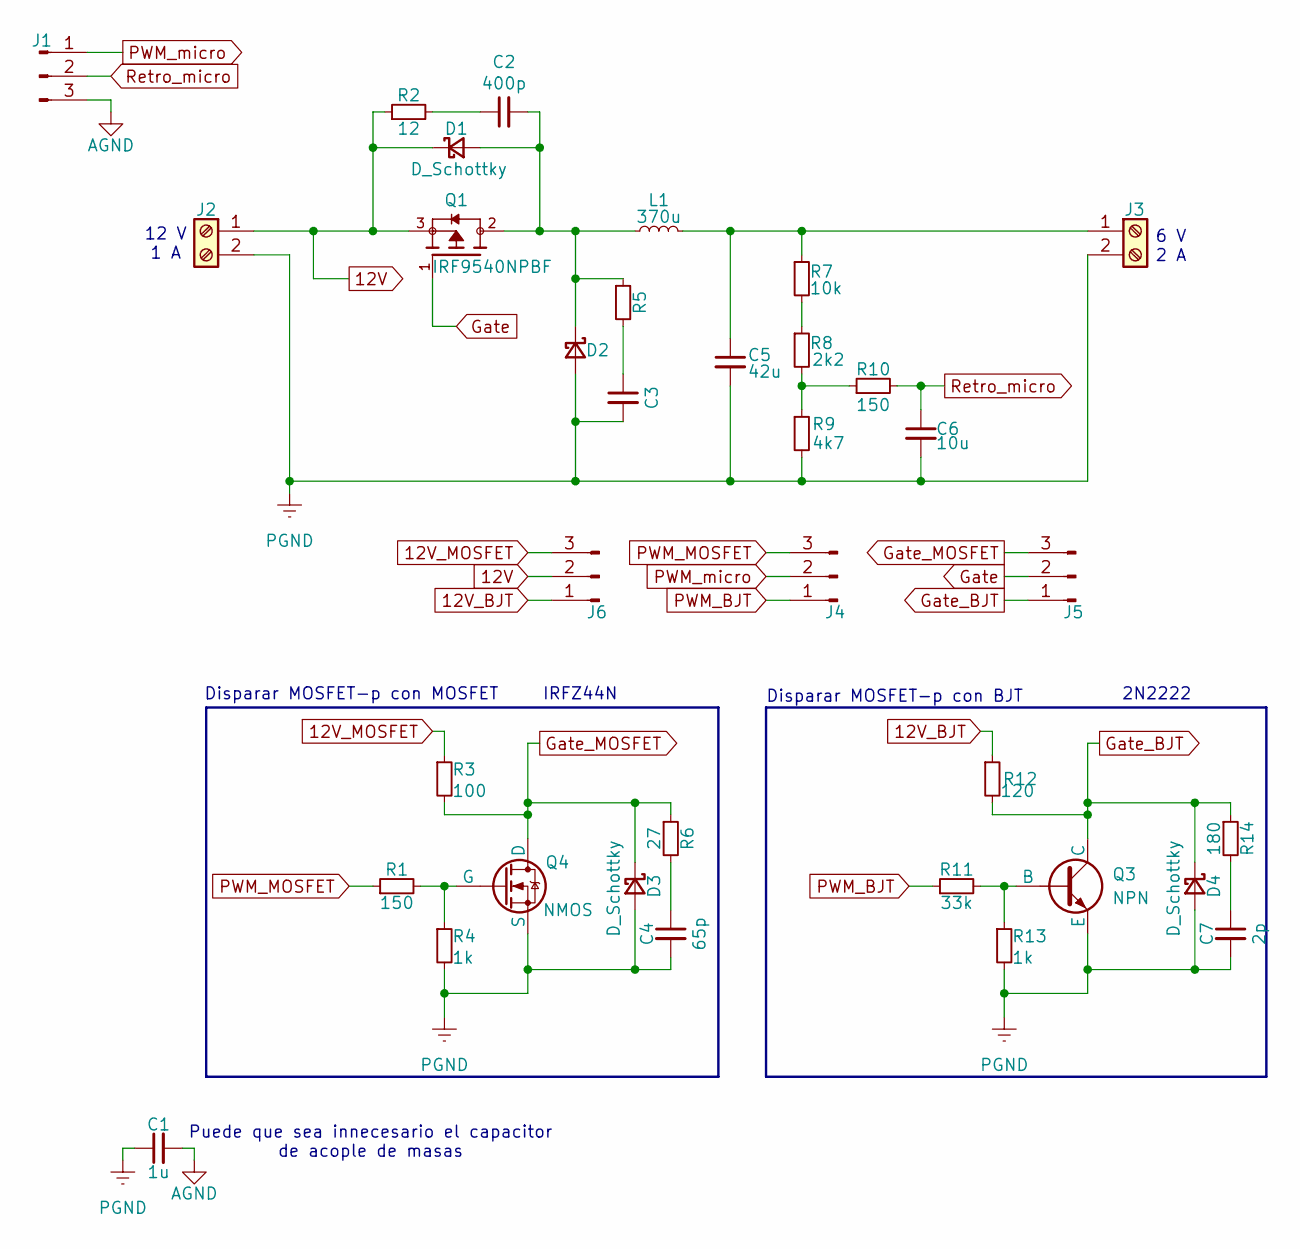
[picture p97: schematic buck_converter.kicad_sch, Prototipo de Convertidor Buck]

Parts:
C1: 1u; C_Disc_D3.8mm_W2.6mm_P2.50mm
C2: 400p; C_Disc_D3.8mm_W2.6mm_P2.50mm
C3: C_Disc_D3.8mm_W2.6mm_P2.50mm
C4: 65p; C_Disc_D3.8mm_W2.6mm_P2.50mm
C5: 42u; C_Disc_D3.8mm_W2.6mm_P2.50mm
C6: 10u; C_Disc_D3.8mm_W2.6mm_P2.50mm
C7: 2p; C_Disc_D3.8mm_W2.6mm_P2.50mm
D1, D2, D3, D4: D_Schottky; D_DO-34_SOD68_P7.62mm_Horizontal
J1, J4, J5, J6: Conn_01x03_Pin; PinHeader_1x03_P2.54mm_Vertical
J2, J3: Screw_Terminal_01x02; TerminalBlock_Phoenix_MKDS-1,5-2-5.08_1x02_P5.08mm_Horizont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
L1: 370u; L_Axial_L16.0mm_D6.3mm_P25.40mm_Horizontal_Fastron_VHBCC
Q1: IRF9540NPBF; TO254P470X1000X2000-3P; PARTREV B
Q3: NPN; TO-92_Inline_Wide
Q4: NMOS; TO-220-3_Vertical
R1, R10: 150; R_Axial_DIN0207_L6.3mm_D2.5mm_P7.62mm_Horizontal
R2: 12; R_Axial_DIN0207_L6.3mm_D2.5mm_P7.62mm_Horizontal
R3: 100; R_Axial_DIN0207_L6.3mm_D2.5mm_P7.62mm_Horizontal
R4, R13: 1k; R_Axial_DIN0207_L6.3mm_D2.5mm_P7.62mm_Horizontal
R5: R_Axial_DIN0207_L6.3mm_D2.5mm_P7.62mm_Horizontal
R6: 27; R_Axial_DIN0207_L6.3mm_D2.5mm_P7.62mm_Horizontal
R7: 10k; R_Axial_DIN0207_L6.3mm_D2.5mm_P7.62mm_Horizontal
R8: 2k2; R_Axial_DIN0207_L6.3mm_D2.5mm_P7.62mm_Horizontal
R9: 4k7; R_Axial_DIN0207_L6.3mm_D2.5mm_P7.62mm_Horizontal
R11: 33k; R_Axial_DIN0207_L6.3mm_D2.5mm_P7.62mm_Horizontal
R12: 120; R_Axial_DIN0207_L6.3mm_D2.5mm_P7.62mm_Horizontal
R14: 180; R_Axial_DIN0207_L6.3mm_D2.5mm_P7.62mm_Horizontal

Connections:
12V: D1.1 (K), J2.1, J6.2, Q1.3, R2.1
12V_BJT: J6.1, R12.1
12V_MOSFET: J6.3, R3.1
AGND: C1.2, J1.3
Gate: J5.2, Q1.1
Gate_BJT: D4.1 (K), J5.1, Q3.3 (C), R12.2, R14.1
Gate_MOSFET: D3.1 (K), J5.3, Q4.2 (D), R3.2, R6.1
unnamed: C2.1, R2.2
unnamed: C3.1, R5.2
unnamed: C4.1, R6.2
unnamed: C7.1, R14.2
unnamed: C2.2, D1.2 (A), D2.1 (K), L1.1, Q1.2, R5.1
unnamed: C5.1, J3.1, L1.2, R7.1
unnamed: Q3.2 (B), R11.2, R13.1
unnamed: Q4.1 (G), R1.2, R4.1
unnamed: R7.2, R8.1
unnamed: R8.2, R9.1, R10.1
PGND: C1.1, C3.2, C4.2, C5.2, C6.2, C7.2, D2.2 (A), D3.2 (A), D4.2 (A), J2.2, J3.2, Q3.1 (E), Q4.3 (S), R4.2, R9.2, R13.2
PWM_BJT: J4.1, R11.1
PWM_MOSFET: J4.3, R1.1
PWM_micro: J1.1, J4.2
Retro_micro: C6.1, J1.2, R10.2

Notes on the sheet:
Puede que sea innecesario el capacitor de acople de masas
2N2222
IRFZ44N
6 V 2 A
Disparar MOSFET-p con BJT
12 V 1 A
Disparar MOSFET-p con MOSFET

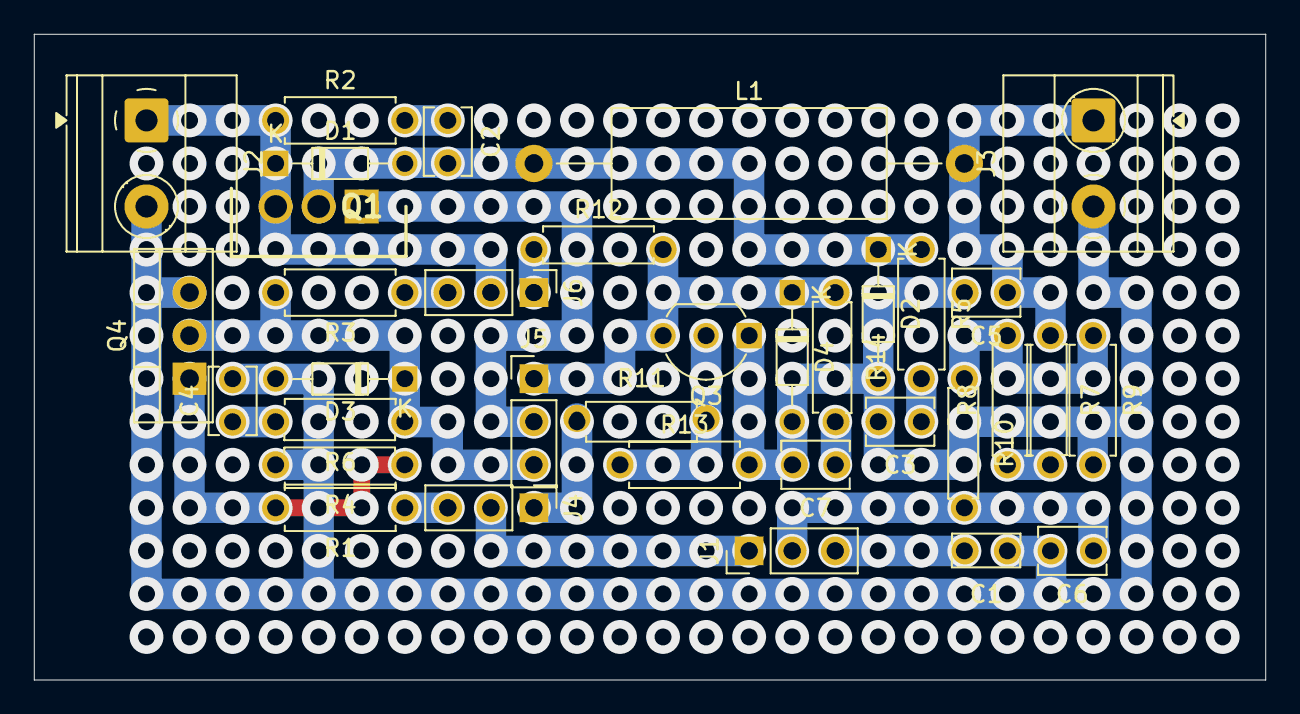
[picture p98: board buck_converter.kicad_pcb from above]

Board: 2 copper layers, 72.7 x 38.1 mm, 35 parts (0 on the bottom side), 22 nets.

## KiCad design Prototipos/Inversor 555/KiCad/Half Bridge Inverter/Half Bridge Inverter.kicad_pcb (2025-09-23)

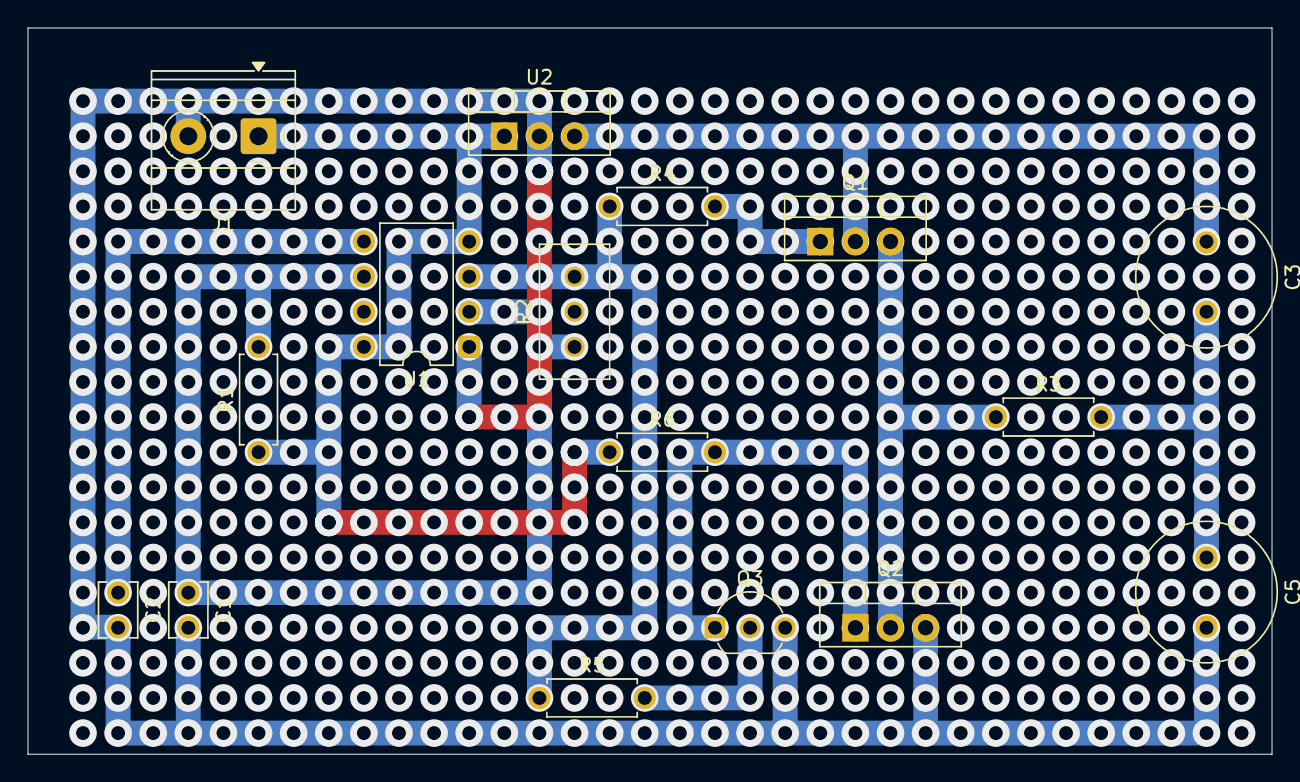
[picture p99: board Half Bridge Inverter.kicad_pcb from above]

Board: 2 copper layers, 90.0 x 52.5 mm, 16 parts (0 on the bottom side), 11 nets.

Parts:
C1: 10u; C_Disc_D3.8mm_W2.6mm_P2.50mm
C2: 0.01u; C_Disc_D3.8mm_W2.6mm_P2.50mm
C3, C5: 1000u; C_Radial_D10.0mm_H16.0mm_P5.00mm
J1: Screw_Terminal_01x02; TerminalBlock_Phoenix_MKDS-1,5-2-5.08_1x02_P5.08mm_Horizont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
Q1, Q2: IRF4905; TO-220-3_Vertical
Q3: BC548; TO-92_Inline_Wide
R1: 100k; R_Axial_DIN0207_L6.3mm_D2.5mm_P7.62mm_Horizontal
R2: 1443; Potentiometer_Bourns_3296W_Vertical
R3: Carga; R_Axial_DIN0207_L6.3mm_D2.5mm_P7.62mm_Horizontal
R4: 100; R_Axial_DIN0207_L6.3mm_D2.5mm_P7.62mm_Horizontal
R5: 5,6k; R_Axial_DIN0207_L6.3mm_D2.5mm_P7.62mm_Horizontal
R6: 120; R_Axial_DIN0207_L6.3mm_D2.5mm_P7.62mm_Horizontal
U1: TLC555xD; DIP-8_W7.62mm
U2: LM7809_TO220; TO-220-3_Vertical

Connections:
555: R2.1, R4.1, R5.1, U1.3 (Q)
Earth: C1.2, C2.2, C5.2, J1.1, Q2.3 (S), Q3.3 (E), U1.1 (GND), U2.2 (GND)
unnamed: C3.2, C5.1, R3.2
unnamed: C3.1, Q1.2 (D), U2.3 (VO)
unnamed: Q1.1 (G), R4.2
unnamed: Q1.3 (S), Q2.2 (D), R3.1
unnamed: Q2.1 (G), Q3.1 (C), R6.2
unnamed: Q3.2 (B), R5.2
unnamed: C2.1, U1.5 (CV)
unnamed: C1.1, R1.2, R2.3, U1.2 (TR), U1.6 (THR)
VDD: J1.2, R1.1, R6.1, U1.4 (R), U1.8 (VCC), U2.1 (VI)

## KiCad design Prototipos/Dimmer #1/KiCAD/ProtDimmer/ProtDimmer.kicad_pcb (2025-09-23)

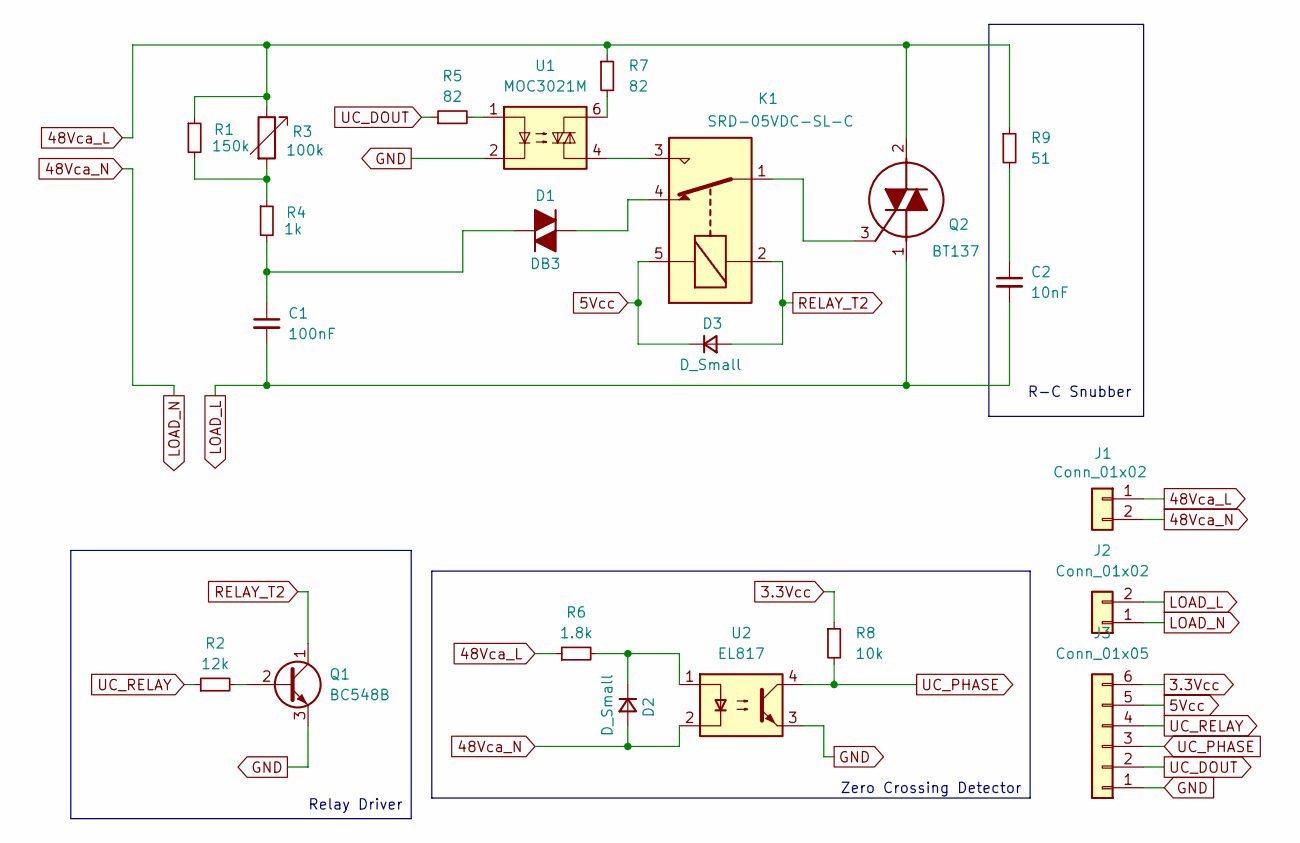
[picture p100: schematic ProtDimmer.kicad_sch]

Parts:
C1: 100nF; C_Disc_D10.5mm_W5.0mm_P7.50mm
C2: 10nF; C_Disc_D10.5mm_W5.0mm_P7.50mm
D1: DB3; D_DO-35_SOD27_P7.62mm_Horizontal
D2, D3: D_Small; D_DO-41_SOD81_P7.62mm_Horizontal
J1, J2: Conn_01x02; TerminalBlock_Phoenix_MKDS-1,5-2-5.08_1x02_P5.08mm_Horizont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
J3: Conn_01x05; PinHeader_1x06_P2.54mm_Vertical
K1: SRD-05VDC-SL-C; Relay_SPDT_SANYOU_SRD_Series_Form_C
Q1: BC548B; TO-92_Inline_Wide
Q2: BT137; TO254P470X1000X2000-3P; Mouser Part Number 771-BT137-600E
R1: 150k; R_Axial_DIN0207_L6.3mm_D2.5mm_P7.62mm_Horizontal
R2: 12k; R_Axial_DIN0207_L6.3mm_D2.5mm_P7.62mm_Horizontal
R3: 100k; Potentiometer_Alps_RK163_Single_Horizontal
R4: 1k; R_Axial_DIN0207_L6.3mm_D2.5mm_P7.62mm_Horizontal
R5, R7: 82; R_Axial_DIN0207_L6.3mm_D2.5mm_P7.62mm_Horizontal
R6: 1.8k; R_Axial_DIN0207_L6.3mm_D2.5mm_P7.62mm_Horizontal
R8: 10k; R_Axial_DIN0207_L6.3mm_D2.5mm_P7.62mm_Horizontal
R9: 51; R_Axial_DIN0207_L6.3mm_D2.5mm_P7.62mm_Horizontal
U1: MOC3021M; DIP762W45P254L889H508Q6
U2: EL817; DIP-4_W7.62mm

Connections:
3.3Vcc: J3.6, R8.1
5Vcc: D3.1 (K), J3.5, K1.5
48Vca_L: J1.1, Q2.2 (MT2), R1.1, R3.1, R3.3, R6.1, R7.1, R9.1
48Vca_N: D2.2 (A), J1.2, J2.1, U2.2
GND: J3.1, Q1.3 (E), U1.2, U2.3
LOAD_L: C1.2, C2.2, J2.2, Q2.1 (MT1)
unnamed: C2.1, R9.2
unnamed: D1.2 (A), K1.4
unnamed: C1.1, D1.1 (K), R4.2
unnamed: D2.1 (K), R6.2, U2.1
unnamed: K1.3, U1.4
unnamed: Q1.2 (B), R2.2
unnamed: K1.1, Q2.3 (G)
unnamed: R1.2, R3.2, R4.1
unnamed: R5.2, U1.1
unnamed: R7.2, U1.6
RELAY_T2: D3.2 (A), K1.2, Q1.1 (C)
UC_DOUT: J3.2, R5.1
UC_PHASE: J3.3, R8.2, U2.4
UC_RELAY: J3.4, R2.1

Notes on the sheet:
R-C Snubber
Zero Crossing Detector
Relay Driver

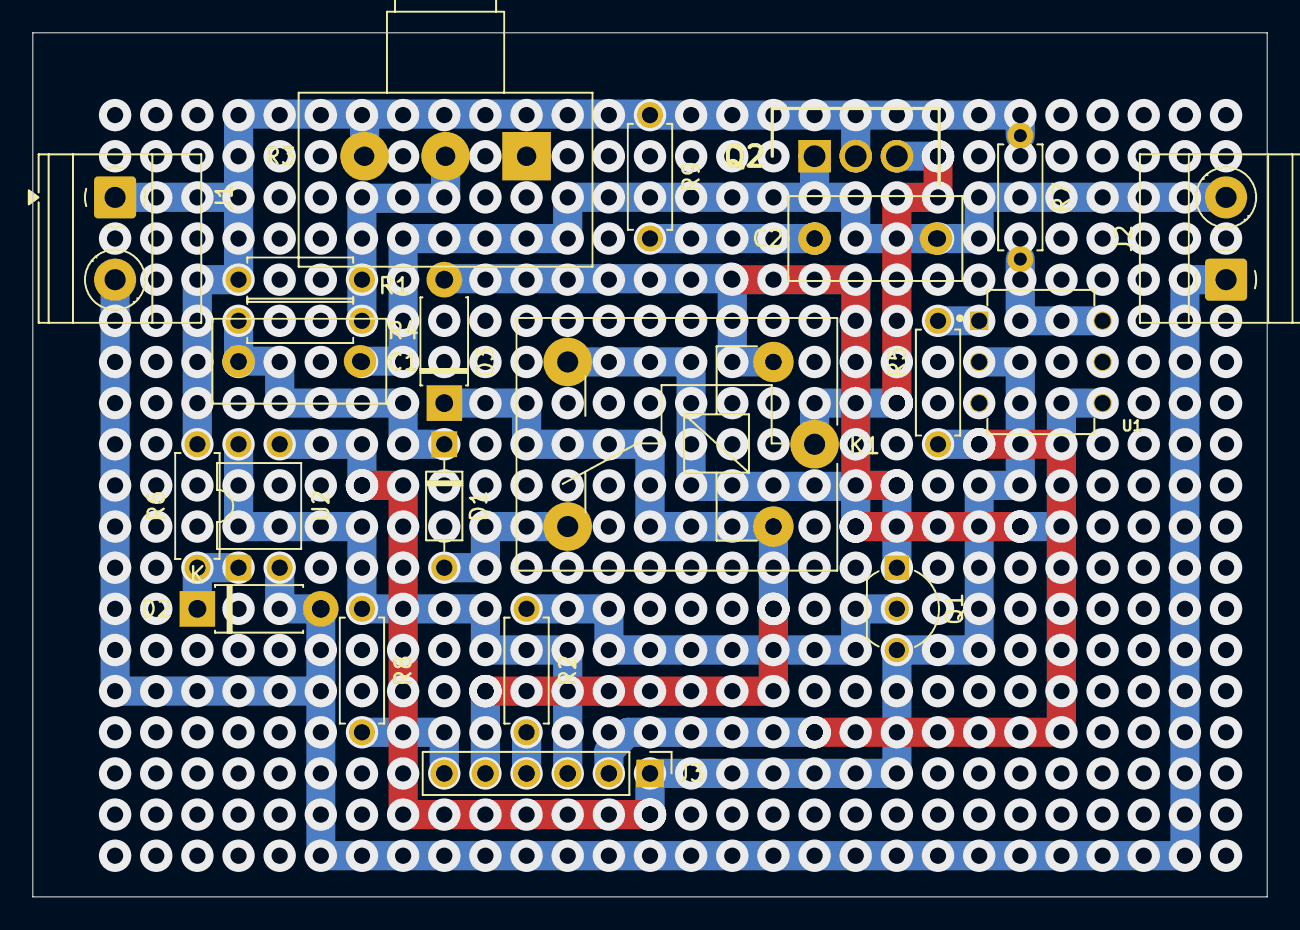
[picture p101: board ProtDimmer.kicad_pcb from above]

Board: 2 copper layers, 76.2 x 53.3 mm, 22 parts (0 on the bottom side), 20 nets.

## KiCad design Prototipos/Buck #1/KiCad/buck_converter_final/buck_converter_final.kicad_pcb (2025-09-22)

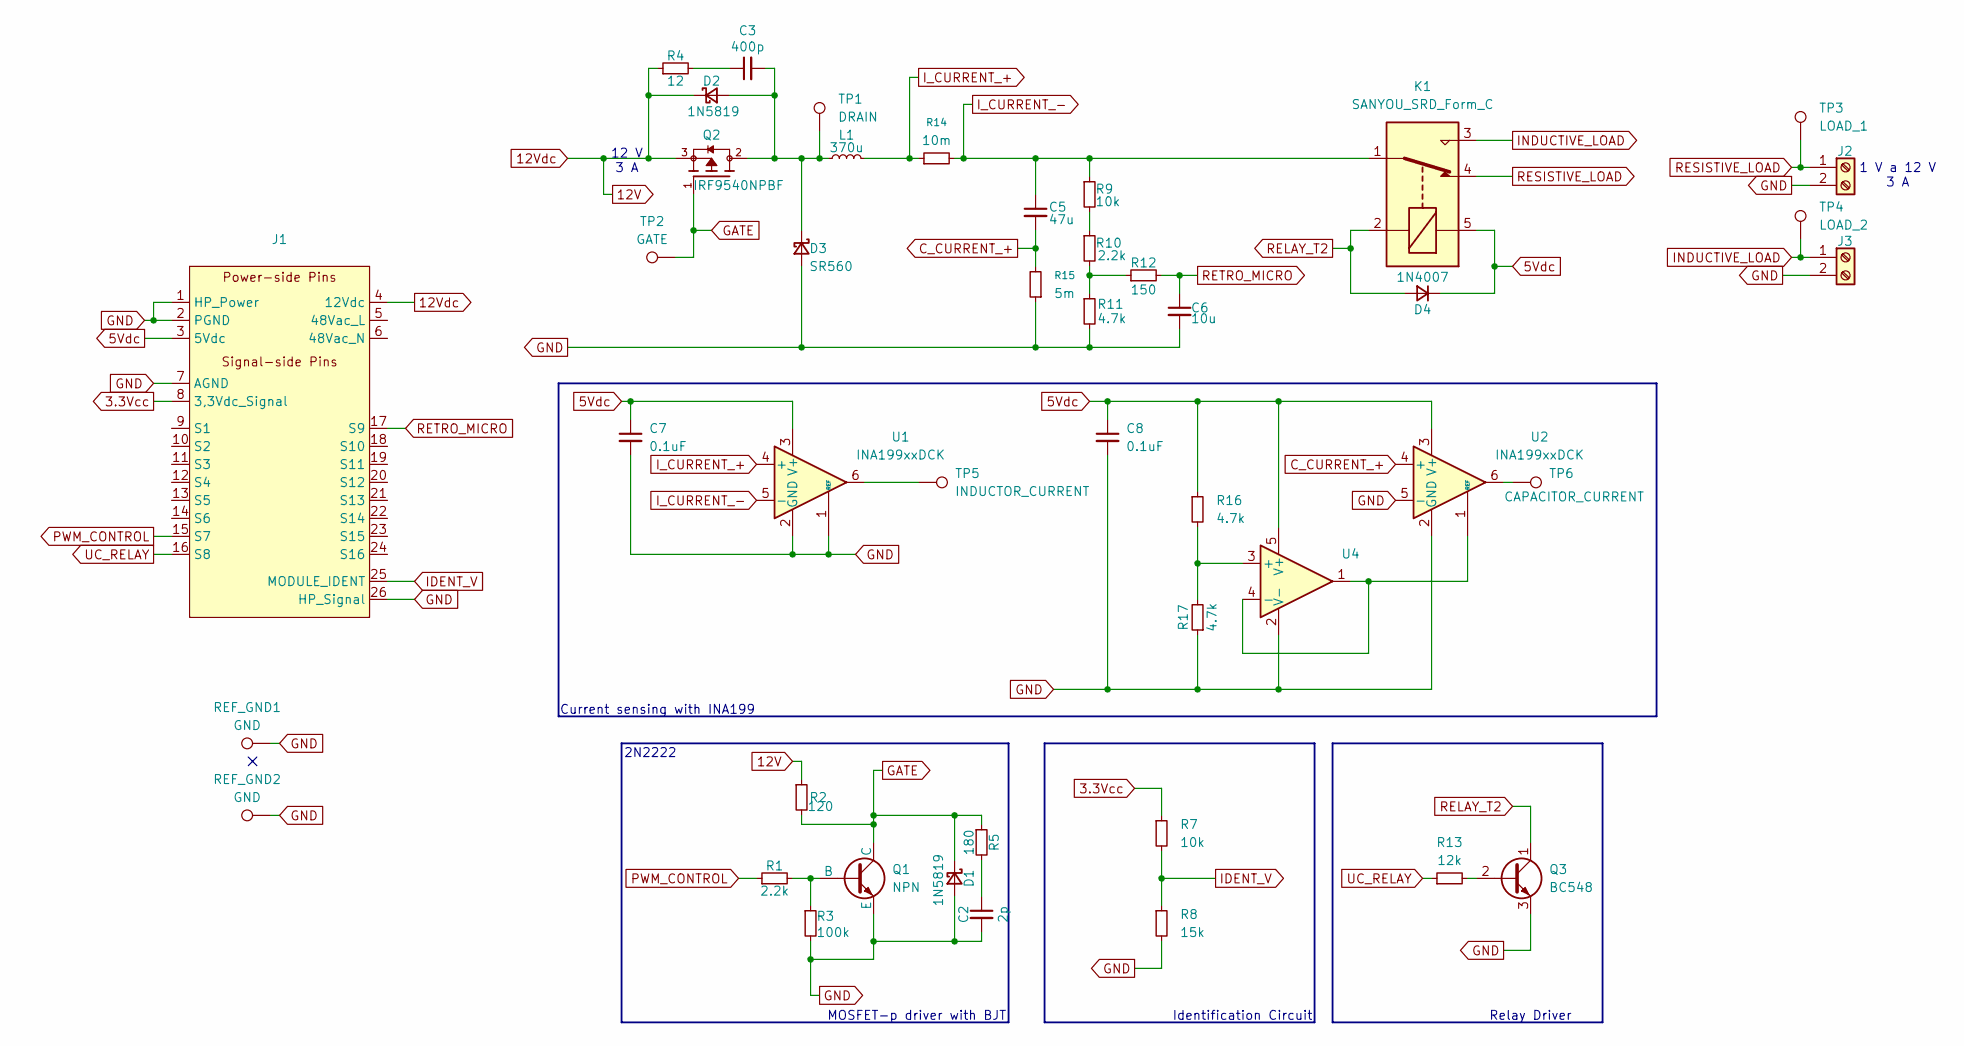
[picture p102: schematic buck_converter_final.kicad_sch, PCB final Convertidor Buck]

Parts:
C2: 2p; C_Disc_D3.8mm_W2.6mm_P2.50mm
C3: 400p; C_Disc_D3.8mm_W2.6mm_P2.50mm
C5: 47u; C_Radial_D5.0mm_H11.0mm_P2.00mm
C6: 10u; C_Radial_D4.0mm_H7.0mm_P1.50mm
C7, C8: 0.1uF; C_0805_2012Metric_Pad1.18x1.45mm_HandSolder
D1, D2: 1N5819; D_DO-34_SOD68_P7.62mm_Horizontal
D3: SR560; D_DO-201AD_P12.70mm_Horizontal
D4: 1N4007; D_DO-41_SOD81_P7.62mm_Horizontal
J1: BUS_PCIE_x4_NSH
J2, J3: Screw_Terminal_01x02; TerminalBlock_Phoenix_MKDS-1,5-2-5.08_1x02_P5.08mm_Horizont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
K1: SANYOU_SRD_Form_C; Relay_SPDT_SANYOU_SRD_Series_Form_C
L1: 370u; L_Toroid_Vertical_L16.0mm_W8.0mm_P7.62mm
Q1: NPN; TO-92_Inline_Wide
Q2: IRF9540NPBF; TO-220-3_Horizontal_TabDown; PARTREV B
Q3: BC548; TO-92_Inline_Wide
R1, R10: 2.2k; R_Axial_DIN0207_L6.3mm_D2.5mm_P7.62mm_Horizontal
R2: 120; R_Axial_DIN0207_L6.3mm_D2.5mm_P7.62mm_Horizontal
R3: 100k; R_Axial_DIN0207_L6.3mm_D2.5mm_P7.62mm_Horizontal
R4: 12; R_Axial_DIN0207_L6.3mm_D2.5mm_P7.62mm_Horizontal
R5: 180; R_Axial_DIN0207_L6.3mm_D2.5mm_P7.62mm_Horizontal
R7, R9: 10k; R_Axial_DIN0207_L6.3mm_D2.5mm_P7.62mm_Horizontal
R8: 15k; R_Axial_DIN0207_L6.3mm_D2.5mm_P7.62mm_Horizontal
R11: 4.7k; R_Axial_DIN0207_L6.3mm_D2.5mm_P7.62mm_Horizontal
R12: 150; R_Axial_DIN0207_L6.3mm_D2.5mm_P7.62mm_Horizontal
R13: 12k; R_Axial_DIN0207_L6.3mm_D2.5mm_P7.62mm_Horizontal
R14: 10m; R_2512_6332Metric_Pad1.40x3.35mm_HandSolder
R15: 5m; R_2512_6332Metric_Pad1.40x3.35mm_HandSolder
R16, R17: 4.7k; R_0603_1608Metric_Pad0.98x0.95mm_HandSolder
REF_GND1, REF_GND2: GND; TestPoint_Loop_D1.80mm_Drill1.0mm_Beaded
TP1: DRAIN; TestPoint_Loop_D1.80mm_Drill1.0mm_Beaded
TP2: GATE; TestPoint_Loop_D1.80mm_Drill1.0mm_Beaded
TP3: LOAD_1; TestPoint_Loop_D1.80mm_Drill1.0mm_Beaded
TP4: LOAD_2; TestPoint_Loop_D1.80mm_Drill1.0mm_Beaded
TP5: INDUCTOR_CURRENT; TestPoint_Loop_D1.80mm_Drill1.0mm_Beaded
TP6: CAPACITOR_CURRENT; TestPoint_Loop_D1.80mm_Drill1.0mm_Beaded
U1, U2: INA199xxDCK; SOT-363_SC-70-6
U4: TL071HIDBVR; SOT23_DBV_5_TEX-M

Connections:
3.3Vcc: J1.8 (3,3Vdc_Signal), R7.1
5Vdc: C7.1, C8.1, D4.1 (K), J1.3 (5Vdc), K1.5, R16.1, U1.3 (V+), U2.3 (V+), U4.5 (V+)
12V: D2.1 (K), J1.4 (12Vdc), Q2.3, R2.1, R4.1
C_CURRENT_+: C5.2, R15.2, U2.4 (+)
GATE: D1.1 (K), Q1.3 (C), Q2.1, R2.2, R5.1, TP2.1
GND: C2.2, C6.2, C7.2, C8.2, D1.2 (A), D3.2 (A), J1.1 (HP_Power), J1.2 (PGND), J1.7 (AGND), J1.26 (HP_Signal), J2.2, J3.2, Q1.1 (E), Q3.3 (E), R3.2, R8.2, R11.2, R15.1, R17.1, REF_GND1.1, REF_GND2.1, U1.1 (REF), U1.2 (GND), U2.2 (GND), U2.5 (-), U4.2 (V-)
IDENT_V: J1.25 (MODULE_IDENT), R7.2, R8.1
INDUCTIVE_LOAD: J3.1, K1.3, TP4.1
I_CURRENT_+: L1.2, R14.1, U1.4 (+)
I_CURRENT_-: C5.1, K1.1, R9.1, R14.2, U1.5 (-)
unnamed: C2.1, R5.2
unnamed: C3.1, R4.2
unnamed: C3.2, D2.2 (A), D3.1 (K), L1.1, Q2.2, TP1.1
unnamed: Q1.2 (B), R1.2, R3.1
unnamed: Q3.2 (B), R13.2
unnamed: R9.2, R10.1
unnamed: R10.2, R11.1, R12.1
unnamed: TP5.1, U1.6
unnamed: TP6.1, U2.6
unnamed: U2.1 (REF), U4.1, U4.4 (-)
unnamed: R16.2, R17.2, U4.3 (+)
PWM_CONTROL: J1.15 (S7), R1.1
RELAY_T2: D4.2 (A), K1.2, Q3.1 (C)
RESISTIVE_LOAD: J2.1, K1.4, TP3.1
RETRO_MICRO: C6.1, J1.17 (S9), R12.2
UC_RELAY: J1.16 (S8), R13.1

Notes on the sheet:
Current sensing with INA199
MOSFET-p driver with BJT
1 V a 12 V 3 A
Relay Driver
12 V 3 A
Identification Circuit
2N2222

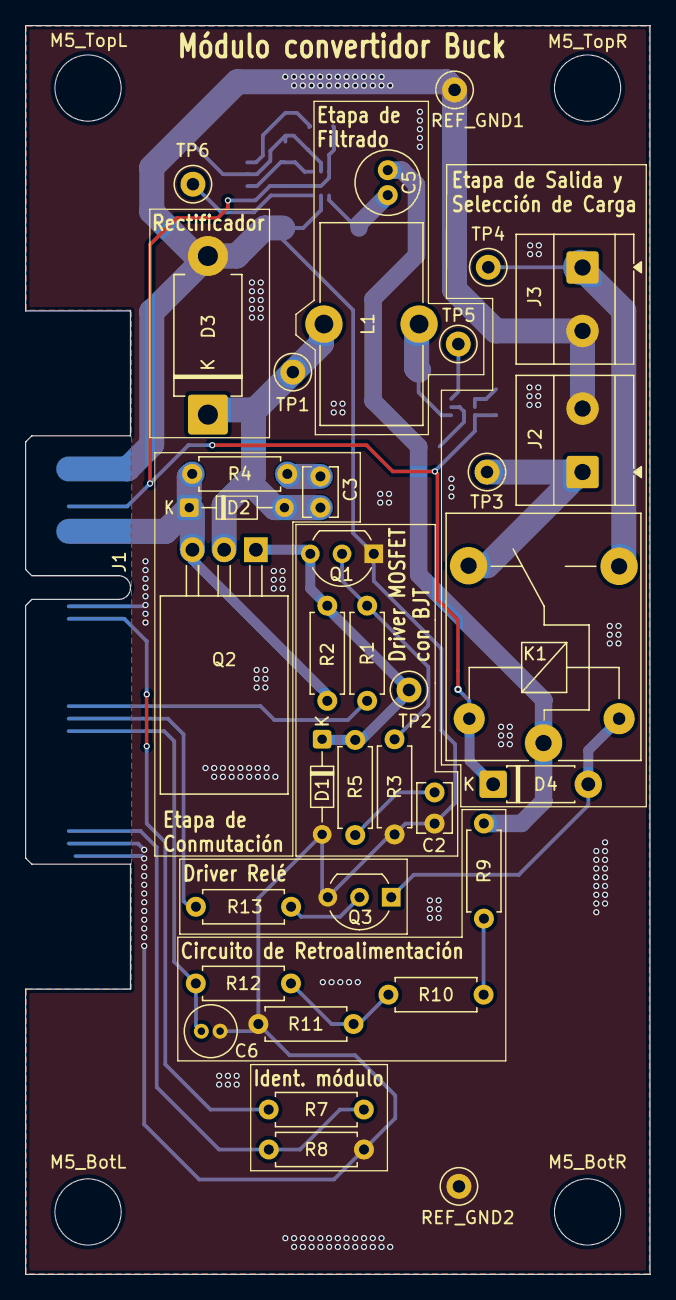
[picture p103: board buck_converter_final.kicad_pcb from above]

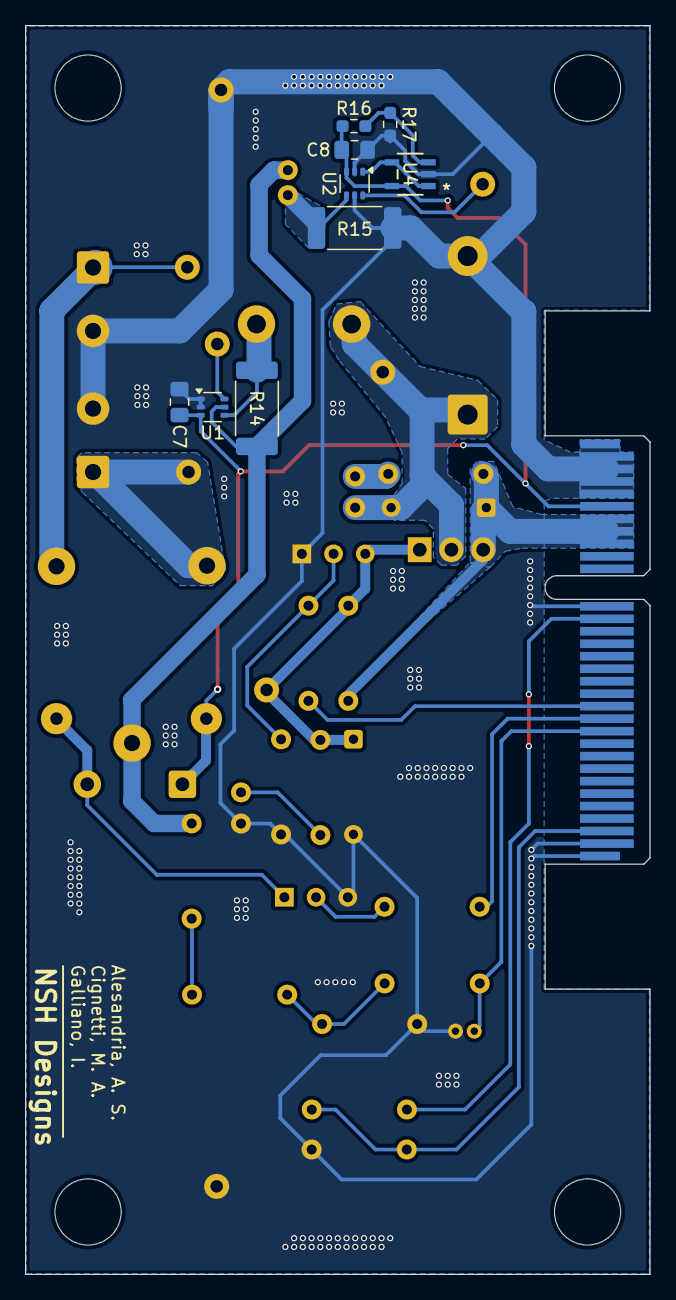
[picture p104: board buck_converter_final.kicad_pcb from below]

Board: 2 copper layers, 50.0 x 100.0 mm, 49 parts (9 on the bottom side), 26 nets.

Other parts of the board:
M5_BotL, M5_BotR, M5_TopL, M5_TopR: MountingHole_5.3mm_M5

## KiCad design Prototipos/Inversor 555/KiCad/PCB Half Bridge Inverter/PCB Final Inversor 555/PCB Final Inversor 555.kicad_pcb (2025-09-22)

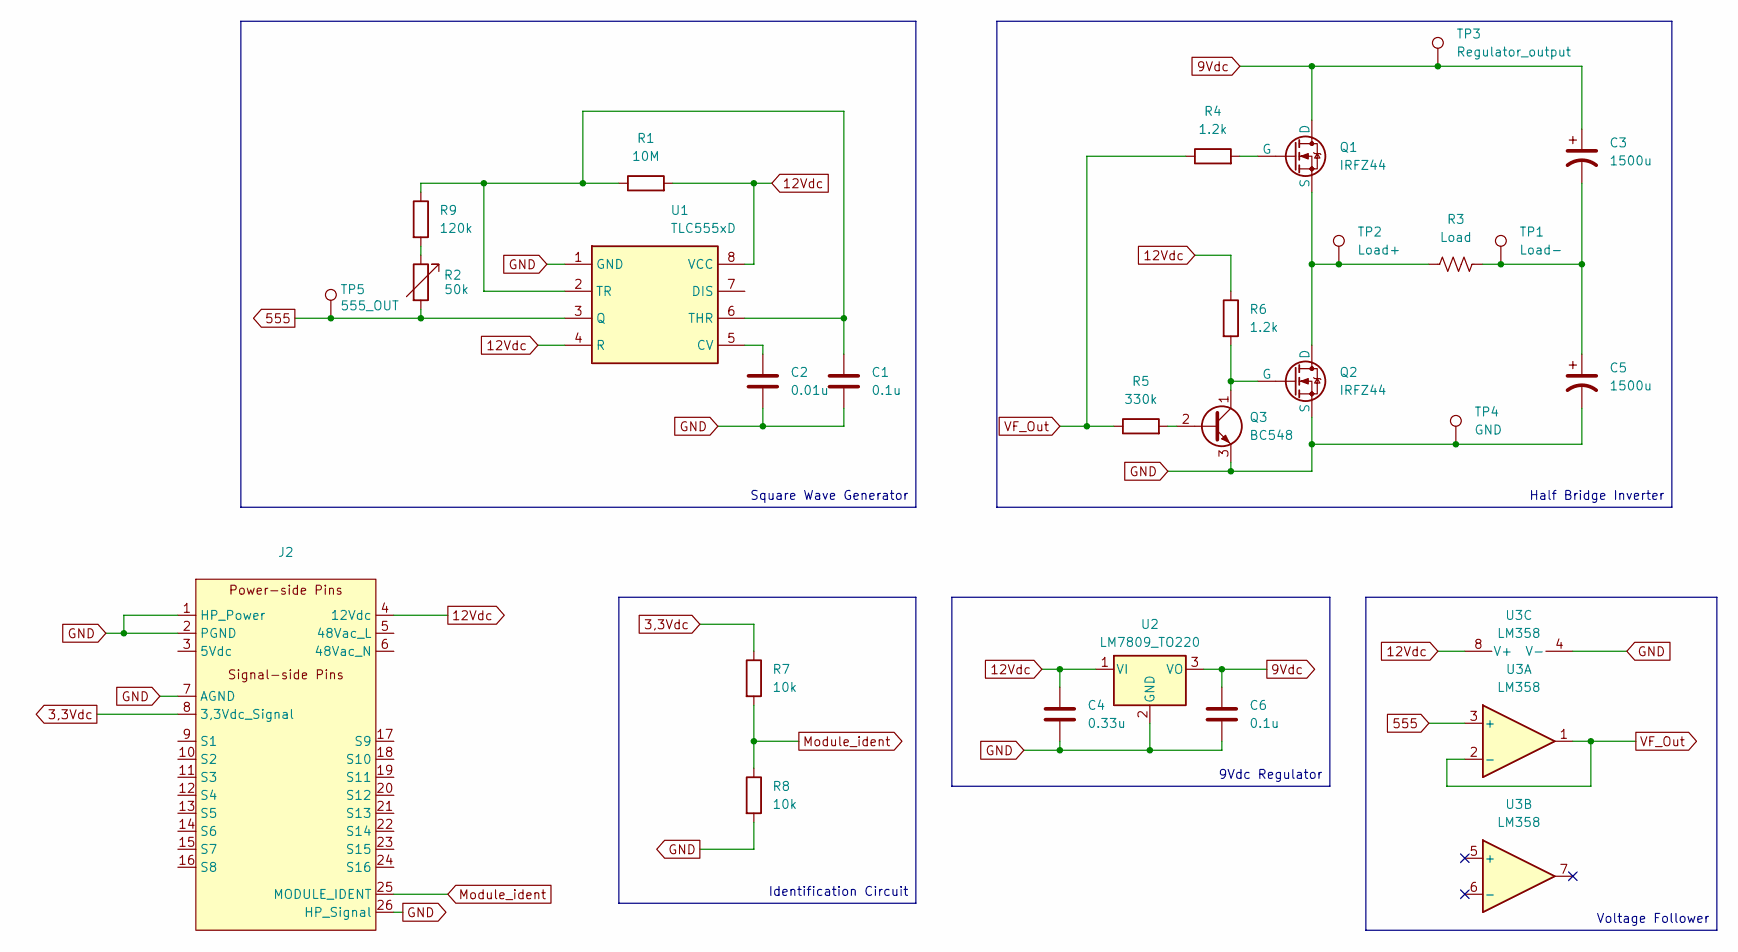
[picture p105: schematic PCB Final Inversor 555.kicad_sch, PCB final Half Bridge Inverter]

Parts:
C1, C6: 0.1u; C_Disc_D3.8mm_W2.6mm_P2.50mm
C2: 0.01u; C_Disc_D3.8mm_W2.6mm_P2.50mm
C3, C5: 1500u; C_Radial_D10.0mm_H16.0mm_P5.00mm
C4: 0.33u; C_Disc_D3.8mm_W2.6mm_P2.50mm
J2: BUS_PCIE_x4_NSH
Q1, Q2: IRFZ44; TO-220-3_Horizontal_TabDown
Q3: BC548; TO-92_Inline_Wide
R1: 10M; R_Axial_DIN0207_L6.3mm_D2.5mm_P7.62mm_Horizontal
R2: 50k; Potentiometer_Alps_RK09K_Single_Vertical
R3: Load; R_Axial_DIN0207_L6.3mm_D2.5mm_P7.62mm_Horizontal
R4, R6: 1.2k; R_Axial_DIN0207_L6.3mm_D2.5mm_P7.62mm_Horizontal
R5: 330k; R_Axial_DIN0207_L6.3mm_D2.5mm_P7.62mm_Horizontal
R7, R8: 10k; R_Axial_DIN0207_L6.3mm_D2.5mm_P7.62mm_Horizontal
R9: 120k; R_Axial_DIN0207_L6.3mm_D2.5mm_P7.62mm_Horizontal
TP1: Load-; TestPoint_Loop_D1.80mm_Drill1.0mm_Beaded
TP2: Load+; TestPoint_Loop_D1.80mm_Drill1.0mm_Beaded
TP3: Regulator_output; TestPoint_Loop_D1.80mm_Drill1.0mm_Beaded
TP4: GND; TestPoint_Loop_D1.80mm_Drill1.0mm_Beaded
TP5: 555_OUT; TestPoint_Loop_D1.80mm_Drill1.0mm_Beaded
U1: TLC555xD; DIP-8_W7.62mm
U2: LM7809_TO220; TO-220-3_Horizontal_TabDown
U3: LM358; DIP-8_W7.62mm

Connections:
3,3Vdc: J2.8 (3,3Vdc_Signal), R7.1
9Vdc: C3.1, C6.1, Q1.1 (D), TP3.1, U2.3 (VO)
12Vdc: C4.1, J2.4 (12Vdc), R1.2, R6.1, U1.4 (R), U1.8 (VCC), U2.1 (VI), U3.8 (V+)
555: R2.2, TP5.1, U1.3 (Q), U3.3 (+)
GND: C1.2, C2.2, C4.2, C5.2, C6.2, J2.1 (HP_Power), J2.2 (PGND), J2.7 (AGND), J2.26 (HP_Signal), Q2.3 (S), Q3.3 (E), R2.MP, R8.2, TP4.1, U1.1 (GND), U2.2 (GND), U3.4 (V-)
Module_ident: J2.25 (MODULE_IDENT), R7.2, R8.1
unnamed: C3.2, C5.1, R3.2, TP1.1
unnamed: Q1.2 (G), R4.2
unnamed: Q1.3 (S), Q2.1 (D), R3.1, TP2.1
unnamed: Q2.2 (G), Q3.1 (C), R6.2
unnamed: Q3.2 (B), R5.2
unnamed: R2.1, R9.2
unnamed: C2.1, U1.5 (CV)
unnamed: C1.1, R1.1, R9.1, U1.2 (TR), U1.6 (THR)
VF_Out: R4.1, R5.1, U3.1, U3.2 (-)

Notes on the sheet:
Identification Circuit
Voltage Follower
Square Wave Generator
9Vdc Regulator
Half Bridge Inverter

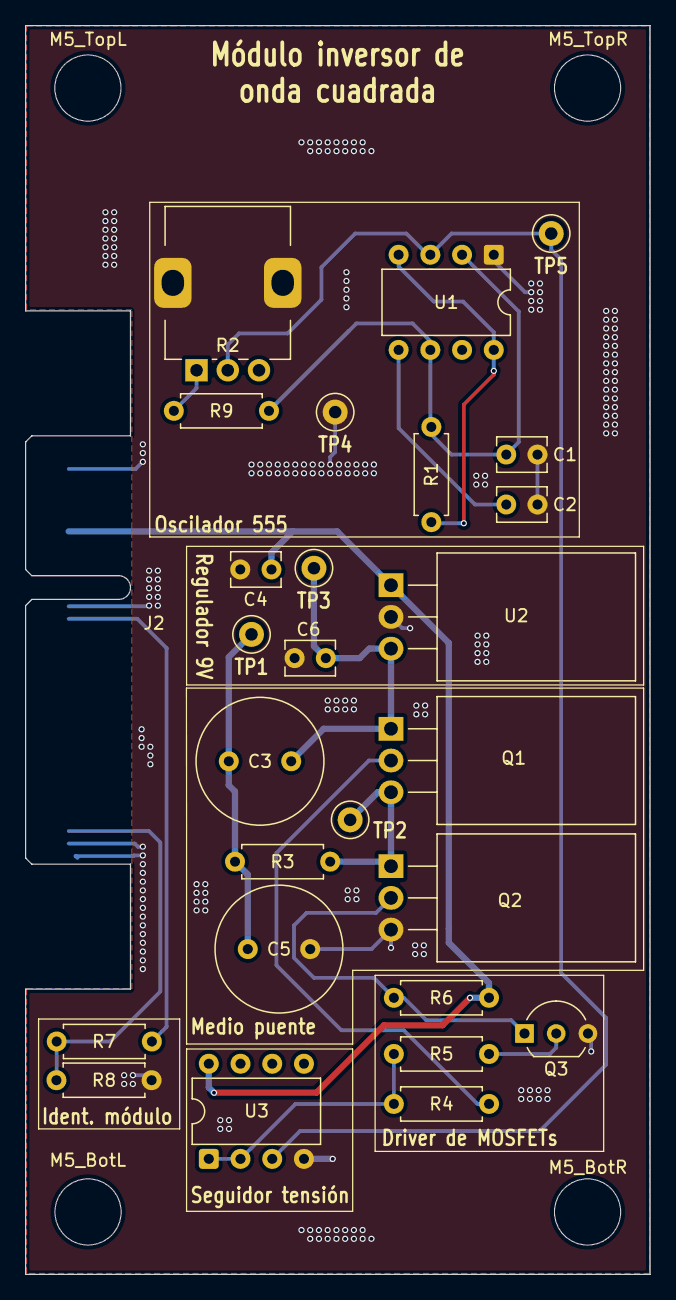
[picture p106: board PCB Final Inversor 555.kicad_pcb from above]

Board: 2 copper layers, 50.0 x 100.0 mm, 31 parts (0 on the bottom side), 15 nets.

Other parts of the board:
M5_BotL, M5_BotR, M5_TopL, M5_TopR: MountingHole_5.3mm_M5

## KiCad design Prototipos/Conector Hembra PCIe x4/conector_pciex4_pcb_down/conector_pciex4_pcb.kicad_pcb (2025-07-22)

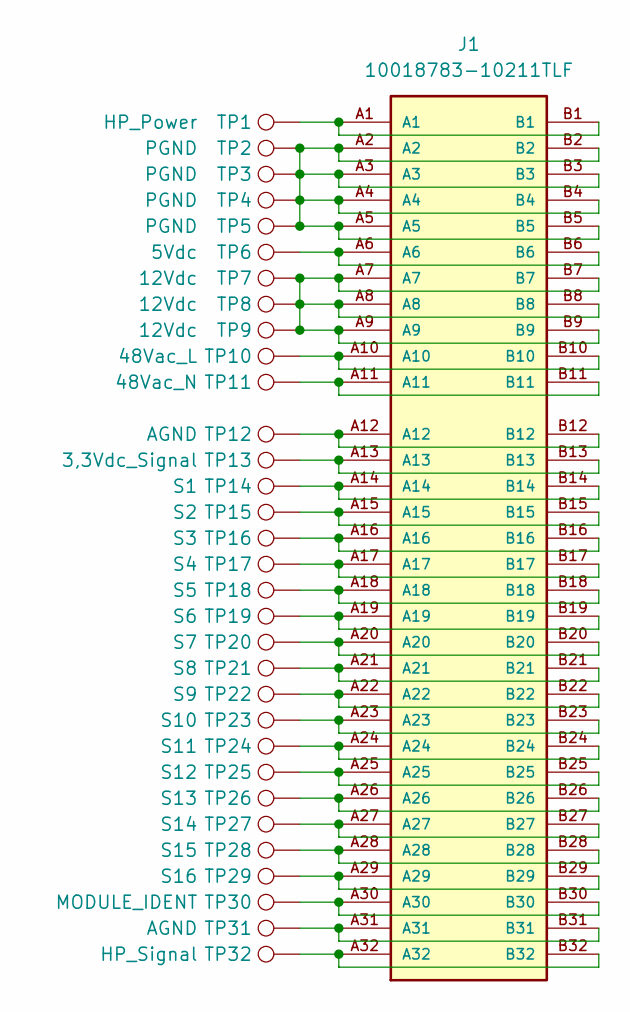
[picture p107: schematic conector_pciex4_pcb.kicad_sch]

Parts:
J1: 10018783-10211TLF; AMPHENOL_10018783-10211TLF; PARTREV AA
TP1: HP_Power; TestPoint_THTPad_D1.5mm_Drill0.7mm
TP2, TP3, TP4, TP5: PGND; TestPoint_THTPad_D1.5mm_Drill0.7mm
TP6: 5Vdc; TestPoint_THTPad_D1.5mm_Drill0.7mm
TP7, TP8, TP9: 12Vdc; TestPoint_THTPad_D1.5mm_Drill0.7mm
TP10: 48Vac_L; TestPoint_THTPad_D1.5mm_Drill0.7mm
TP11: 48Vac_N; TestPoint_THTPad_D1.5mm_Drill0.7mm
TP12, TP31: AGND; TestPoint_THTPad_D1.5mm_Drill0.7mm
TP13: 3,3Vdc_Signal; TestPoint_THTPad_D1.5mm_Drill0.7mm
TP14: S1; TestPoint_THTPad_D1.5mm_Drill0.7mm
TP15: S2; TestPoint_THTPad_D1.5mm_Drill0.7mm
TP16: S3; TestPoint_THTPad_D1.5mm_Drill0.7mm
TP17: S4; TestPoint_THTPad_D1.5mm_Drill0.7mm
TP18: S5; TestPoint_THTPad_D1.5mm_Drill0.7mm
TP19: S6; TestPoint_THTPad_D1.5mm_Drill0.7mm
TP20: S7; TestPoint_THTPad_D1.5mm_Drill0.7mm
TP21: S8; TestPoint_THTPad_D1.5mm_Drill0.7mm
TP22: S9; TestPoint_THTPad_D1.5mm_Drill0.7mm
TP23: S10; TestPoint_THTPad_D1.5mm_Drill0.7mm
TP24: S11; TestPoint_THTPad_D1.5mm_Drill0.7mm
TP25: S12; TestPoint_THTPad_D1.5mm_Drill0.7mm
TP26: S13; TestPoint_THTPad_D1.5mm_Drill0.7mm
TP27: S14; TestPoint_THTPad_D1.5mm_Drill0.7mm
TP28: S15; TestPoint_THTPad_D1.5mm_Drill0.7mm
TP29: S16; TestPoint_THTPad_D1.5mm_Drill0.7mm
TP30: MODULE_IDENT; TestPoint_THTPad_D1.5mm_Drill0.7mm
TP32: HP_Signal; TestPoint_THTPad_D1.5mm_Drill0.7mm

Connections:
unnamed: J1.A1, J1.B1, TP1.1
unnamed: J1.A2, J1.A3, J1.A4, J1.A5, J1.B2, J1.B3, J1.B4, J1.B5, TP2.1, TP3.1, TP4.1, TP5.1
unnamed: J1.A6, J1.B6, TP6.1
unnamed: J1.A7, J1.A8, J1.A9, J1.B7, J1.B8, J1.B9, TP7.1, TP8.1, TP9.1
unnamed: J1.A10, J1.B10, TP10.1
unnamed: J1.A11, J1.B11, TP11.1
unnamed: J1.A12, J1.B12, TP12.1
unnamed: J1.A13, J1.B13, TP13.1
unnamed: J1.A14, J1.B14, TP14.1
unnamed: J1.A15, J1.B15, TP15.1
unnamed: J1.A16, J1.B16, TP16.1
unnamed: J1.A17, J1.B17, TP17.1
unnamed: J1.A18, J1.B18, TP18.1
unnamed: J1.A19, J1.B19, TP19.1
unnamed: J1.A20, J1.B20, TP20.1
unnamed: J1.A21, J1.B21, TP21.1
unnamed: J1.A22, J1.B22, TP22.1
unnamed: J1.A23, J1.B23, TP23.1
unnamed: J1.A24, J1.B24, TP24.1
unnamed: J1.A25, J1.B25, TP25.1
unnamed: J1.A26, J1.B26, TP26.1
unnamed: J1.A27, J1.B27, TP27.1
unnamed: J1.A28, J1.B28, TP28.1
unnamed: J1.A29, J1.B29, TP29.1
unnamed: J1.A30, J1.B30, TP30.1
unnamed: J1.A31, J1.B31, TP31.1
unnamed: J1.A32, J1.B32, TP32.1


Board: 2 copper layers, 14.7 x 39.5 mm, 33 parts (0 on the bottom side), 27 nets.

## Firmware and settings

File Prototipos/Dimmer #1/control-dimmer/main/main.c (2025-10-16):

/**
 * @file main.c
 * @author Mateo Antonio Cignetti (mateo@cignetti.ar)
 * @brief Isolated dimmer control for the dimmer prototype, using two gptimers to avoid blocking tasks
 * @version 1.0
 * @date 2025-05-25
 * 
 * @copyright Copyright (c) 2025
 * 
*/

// IMPORTANT: The prototype's relay pin must be shorted to 3.3 V for the dimmer to be set in digital control mode.
//            This was not included in this program to keep test components to a minimum.

#include "driver/gpio.h" // GPIO driver
#include "driver/gptimer.h" // Driver for the gptimers
#include "esp_attr.h" // Needed for IRAM_ATTR (needed for interrupt handler)
#include "esp_log.h" // ESP-IDF logging library
#include "esp_adc/adc_oneshot.h" // ADC Oneshot driver
#include "freertos/FreeRTOS.h" // FreeRTOS general library
#include "freertos/task.h" // FreeRTOS task library


// Generates a test 50 Hz square wave signal on the defined pin below,
// to test the dimmer without the need of a real zero crossing detector.
// Only for testing without the dimmer prototype connected.
#define USE_TEST_ZCD_SIGNAL 0

#if USE_TEST_ZCD_SIGNAL
#include "driver/ledc.h"
#define PIN_TEST_ZCD_SIGNAL GPIO_NUM_10
#define TEST_SIGNAL_FREQUENCY 50
#endif
//


#define ESP_INTR_FLAG_DEFAULT 0 // Default interrupt flag
#define PIN_RELAY_OUT GPIO_NUM_4
#define PIN_ZCD_IN GPIO_NUM_2 // Zero crossing detector input pin
#define PIN_TRIAC_OUT GPIO_NUM_41 // TRIAC output pin
#define ADC_READ_CHANNEL ADC_CHANNEL_2 // ADC channel to read (GPIO 3)
#define PULSE_WIDTH_US 25 // Pulse width for driving the triac, in microseconds
#define DIMMER_TIMER_COUNT_DEFAULT 9900 // Turns on TRIAC at 9,9 ms after zero crossing
                                        // (basically starts the dimmer off)
#define ADC_SAMPLING_FREQUENCY 40 // ADC sampling frequency in Hz
#define ALARM_COUNT_MIN 100 // Minimum alarm count for the dimmer
#define ALARM_COUNT_MAX 9900 // Maximum alarm count for the dimmer

static gptimer_handle_t dimmer_wait_timer = NULL; // Handle for the wait timer
static gptimer_handle_t dimmer_pulse_timer = NULL; // Handle for the pulse timer
static adc_oneshot_unit_handle_t adc1_handle = NULL; // Handle for the ADC1 unit
static TaskHandle_t xTaskAdcRead_handle = NULL; // Task handle for the ADC read task

static volatile bool timer_is_running = false; // Aux flag to ensure proper timer operation, additional
                                      // safety measure in case an interrupt happens mid timer
                                      // (shouldn't happen in normal operation)
static uint16_t dimmer_wait_alarm_count = DIMMER_TIMER_COUNT_DEFAULT; // Static variable to store the alarm count



// Callback of the timer that starts waiting after the zero crossing to turn on the TRIAC
static bool dimmer_wait_callback(gptimer_handle_t timer, const gptimer_alarm_event_data_t *edata, void *user_ctx) {
    
    gptimer_stop(timer); // Stop the timer as soon as possible
    gptimer_set_raw_count(timer, 0); // Set the timer count to 0. Very important, if not reset
                                     // the timer will execute the alarm event immediately

    gpio_set_level(PIN_TRIAC_OUT, 1); // Set TRIAC pin high to start the pulse
    
    gptimer_start(dimmer_pulse_timer); // Start the pulse timer
    
    // ESP_DRAM_LOGI("GPTimer", "Alarm callback executed"); // Uncomment this line when needed for debugging

    return true;
}

// Callback of the pulse timer that waits for the pulse to end to turn off the TRIAC.
// The width of the pulse is not very accurate, but it doesn't matter, the TRIAC will turn on
// anyways. I tried using low level functions for the GPIO set level, but it didn't make any difference.
// For example: 25 us pulse is actually 29 us, accuracy gets worse when the pulse is shorter.
static bool dimmer_pulse_callback(gptimer_handle_t timer, const gptimer_alarm_event_data_t *edata, void *user_ctx) {

    gpio_set_level(PIN_TRIAC_OUT, 0); // Set TRIAC pin low to stop the pulse

    gptimer_stop(timer); // Stop the pulse timer
    gptimer_set_raw_count(timer, 0); // Reset the count, again, important. See callback above
    
    timer_is_running = false; // Reset the timer running flag

    return true;
}

// Handler for the zero crossing detector interrupt.
static void IRAM_ATTR zcd_isr_handler(){
    static gptimer_alarm_config_t wait_alarm_config = {
        .flags.auto_reload_on_alarm = false, // Set the auto reload flag to false
    };
    // Checks that the timer is not running, just in case
    if(!timer_is_running) {
        timer_is_running = true; // Set the timer running flag
        
        wait_alarm_config.alarm_count = dimmer_wait_alarm_count; // Set the alarm count to the default value
        gptimer_set_alarm_action(dimmer_wait_timer, &wait_alarm_config);

        gptimer_start(dimmer_wait_timer); // Start the timer
    } else {
        ESP_DRAM_LOGW("ZCD ISR", "Interrupt happened mid timer, check ZCD signal"); // Log a warning if the timer is already running
    }
    
}

// Function to configure the GPIOs (pins, directions, interrupts, etc.)
void configure_gpios(void){
    
    // Configuration for the zero crossing detector pin
    gpio_config_t zcd_pin_conf = {
        .pin_bit_mask = (1ULL << PIN_ZCD_IN),
        .mode = GPIO_MODE_INPUT,
        .pull_up_en = GPIO_PULLUP_ENABLE,
        .pull_down_en = GPIO_PULLDOWN_DISABLE,
        .intr_type = GPIO_INTR_ANYEDGE,
    };
    ESP_ERROR_CHECK(gpio_config(&zcd_pin_conf)); // Apply the configuration

    ESP_ERROR_CHECK(gpio_install_isr_service(ESP_INTR_FLAG_DEFAULT)); // Install ISR service
    ESP_ERROR_CHECK(gpio_isr_handler_add(PIN_ZCD_IN, zcd_isr_handler, NULL)); // Add ISR handler for the ZCD pin

    // Configuration for the TRIAC pin
    // Configuration for the TRIAC and RELAY pins
    gpio_config_t triac_pin_conf = {
        .pin_bit_mask = (1ULL << PIN_TRIAC_OUT) | (1ULL << PIN_RELAY_OUT),
        .mode = GPIO_MODE_OUTPUT,
        .pull_up_en = GPIO_PULLUP_DISABLE,
        .pull_down_en = GPIO_PULLDOWN_ENABLE,
        .intr_type = GPIO_INTR_DISABLE,
    };
    ESP_ERROR_CHECK(gpio_config(&triac_pin_conf)); // Apply the configuration
    gpio_set_level(PIN_RELAY_OUT, 1);
}

// Function to configure the timers
void configure_timers(void){

    // Configuration for both timers (counting up, and 1 us resolution)
    gptimer_config_t gptimer_config = {
        .clk_src = GPTIMER_CLK_SRC_DEFAULT,
        .direction = GPTIMER_COUNT_UP,
        .resolution_hz = 1 * 1000 * 1000,
    };
    // Apply the configuration to both timers
    ESP_ERROR_CHECK(gptimer_new_timer(&gptimer_config, &dimmer_wait_timer)); 
    ESP_ERROR_CHECK(gptimer_new_timer(&gptimer_config, &dimmer_pulse_timer));

    // Configure the alarm count and behaviour for the wait timer
    gptimer_alarm_config_t wait_alarm_config = {
        .alarm_count = DIMMER_TIMER_COUNT_DEFAULT, // Triggers the alarm event when the timer reaches this value
        .flags.auto_reload_on_alarm = false,
    };
    ESP_ERROR_CHECK(gptimer_set_alarm_action(dimmer_wait_timer, &wait_alarm_config));

    // Configure the alarm count and behaviour for the pulse timer
    gptimer_alarm_config_t pulse_alarm_config = {
        .alarm_count = PULSE_WIDTH_US, // Triggers the alarm event when the timer reaches this value
        .flags.auto_reload_on_alarm = false,
    };
    ESP_ERROR_CHECK(gptimer_set_alarm_action(dimmer_pulse_timer, &pulse_alarm_config));

    // Configure callback functions for both timers on alarm event
    gptimer_event_callbacks_t wait_callbacks = {
        .on_alarm = dimmer_wait_callback, 
    };
    gptimer_event_callbacks_t pulse_callbacks = {
        .on_alarm = dimmer_pulse_callback,
    };
    ESP_ERROR_CHECK(gptimer_register_event_callbacks(dimmer_wait_timer, &wait_callbacks, NULL));
    ESP_ERROR_CHECK(gptimer_register_event_callbacks(dimmer_pulse_timer, &pulse_callbacks, NULL));

    // Enable both timers. The timers are not started yet, but are now ready to be started
    ESP_ERROR_CHECK(gptimer_enable(dimmer_wait_timer));
    ESP_ERROR_CHECK(gptimer_enable(dimmer_pulse_timer));
}

// Function to configure the test signal
#if USE_TEST_ZCD_SIGNAL
void configure_test_signal(void){

    // Configure the ledc timer
    ledc_timer_config_t ledc_timer = {
        .speed_mode = LEDC_LOW_SPEED_MODE,
        .timer_num = LEDC_TIMER_0,
        .duty_resolution = LEDC_TIMER_10_BIT,
        .freq_hz = TEST_SIGNAL_FREQUENCY,
        .clk_cfg = LEDC_AUTO_CLK,
    };
    ESP_ERROR_CHECK(ledc_timer_config(&ledc_timer));

    // Configure the ledc channel
    ledc_channel_config_t ledc_channel = {
        .speed_mode = LEDC_LOW_SPEED_MODE,
        .channel = LEDC_CHANNEL_0,
        .intr_type = LEDC_INTR_DISABLE,
        .timer_sel = LEDC_TIMER_0,
        .gpio_num = PIN_TEST_ZCD_SIGNAL,
        .duty = 512, // 50% duty cycle
        .hpoint = 0,
    };
    ESP_ERROR_CHECK(ledc_channel_config(&ledc_channel));
}
#endif

// Function to configure the ADC
void configure_adc(){

    // Configure the ADC1 unit
    adc_oneshot_unit_init_cfg_t adc1_init_config = {
        .unit_id = ADC_UNIT_1,
        .clk_src = ADC_RTC_CLK_SRC_DEFAULT,
        .ulp_mode = ADC_ULP_MODE_DISABLE,
    };
    ESP_ERROR_CHECK(adc_oneshot_new_unit(&adc1_init_config, &adc1_handle)); // Create the ADC handle

    // Configure the ADC channel
    adc_oneshot_chan_cfg_t adc1_channel_config = {
        .atten = ADC_ATTEN_DB_12,
        .bitwidth = ADC_BITWIDTH_12,
    };
    ESP_ERROR_CHECK(adc_oneshot_config_channel(adc1_handle, ADC_READ_CHANNEL, &adc1_channel_config)); // Configure the ADC channel
}

// Function to map the ADC value to the timer alarm count
uint16_t get_mapped_value(uint32_t x, uint16_t in_min, uint16_t in_max, uint16_t out_min, uint16_t out_max) {
    return (x - in_min) * (out_max - out_min) / (in_max - in_min) + out_min;
}

// Task to read the ADC value and update the timer alarm count
void vTaskAdcRead(void *pvParameters){
    int adc_value = 0;
    const int sampling_period = 1000 / ADC_SAMPLING_FREQUENCY; // Calculate the sampling period in milliseconds
    TickType_t xLastWakeTime = xTaskGetTickCount(); // Get the current tick count

    while(true){
        ESP_ERROR_CHECK(adc_oneshot_read(adc1_handle, ADC_READ_CHANNEL, &adc_value)); // Read the ADC value
        ESP_LOGI("ADC", "ADC Value: %d", adc_value); // Print the ADC value
        dimmer_wait_alarm_count = get_mapped_value((uint16_t) adc_value, 0, 4095, ALARM_COUNT_MIN, ALARM_COUNT_MAX); // Map the ADC value to the timer count
        ESP_LOGI("ADC", "Dimmer alarm count: %d", dimmer_wait_alarm_count); // Print the ADC value

        vTaskDelayUntil(&xLastWakeTime, pdMS_TO_TICKS(sampling_period)); // Delay the task for the sampling period
    }
}

// Function to configure the tasks
void configure_tasks(){
    // Create the ADC read task
    xTaskCreate(vTaskAdcRead,
                "ADC Read Task",
                5*2048,
                NULL,
                5,
                &xTaskAdcRead_handle);
}

void app_main(void){
    
    // Configure the test signal if enabled
    #if USE_TEST_ZCD_SIGNAL
    configure_test_signal();
    #endif
    //
    //configure_adc(); // Configure the ADC
    //configure_tasks(); // Configure the tasks

    configure_timers(); // Configure the timers
    configure_gpios(); // Configure the GPIOs
}

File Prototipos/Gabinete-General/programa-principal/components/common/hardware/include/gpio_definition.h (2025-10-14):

#ifndef GPIO_DEFINITION_H
#define GPIO_DEFINITION_H

#include "soc/gpio_num.h"
#include "hal/adc_types.h"

#define PIN_HP_POWER GPIO_NUM_35
#define PIN_HP_SIGNAL GPIO_NUM_42
#define PIN_MODULE_IDENT GPIO_NUM_3

#define ADC_MODULE_IDENT_UNIT ADC_UNIT_1
#define ADC_MODULE_IDENT_CHANNEL ADC_CHANNEL_2

#define PIN_S1 GPIO_NUM_4
#define PIN_S2 GPIO_NUM_5
#define PIN_S3 GPIO_NUM_6
#define PIN_S4 GPIO_NUM_7
#define PIN_S5 GPIO_NUM_15
#define PIN_S6 GPIO_NUM_16
#define PIN_S7 GPIO_NUM_17
#define PIN_S8 GPIO_NUM_18
#define PIN_S9 GPIO_NUM_8
#define PIN_S10 GPIO_NUM_36
#define PIN_S11 GPIO_NUM_37
#define PIN_S12 GPIO_NUM_38
#define PIN_S13 GPIO_NUM_39
#define PIN_S14 GPIO_NUM_40
#define PIN_S15 GPIO_NUM_41
#define PIN_S16 GPIO_NUM_2

#define ADC_S1_UNIT ADC_UNIT_1
#define ADC_S1_CHANNEL ADC_CHANNEL_3
#define ADC_S2_UNIT ADC_UNIT_1
#define ADC_S2_CHANNEL ADC_CHANNEL_4
#define ADC_S3_UNIT ADC_UNIT_1
#define ADC_S3_CHANNEL ADC_CHANNEL_5
#define ADC_S4_UNIT ADC_UNIT_1
#define ADC_S4_CHANNEL ADC_CHANNEL_6
#define ADC_S5_UNIT ADC_UNIT_2
#define ADC_S5_CHANNEL ADC_CHANNEL_4
#define ADC_S6_UNIT ADC_UNIT_2
#define ADC_S6_CHANNEL ADC_CHANNEL_5
#define ADC_S7_UNIT ADC_UNIT_2
#define ADC_S7_CHANNEL ADC_CHANNEL_6
#define ADC_S8_UNIT ADC_UNIT_2
#define ADC_S8_CHANNEL ADC_CHANNEL_7
#define ADC_S9_UNIT ADC_UNIT_1
#define ADC_S9_CHANNEL ADC_CHANNEL_7
#define ADC_S16_UNIT ADC_UNIT_1
#define ADC_S16_CHANNEL ADC_CHANNEL_1

#define PIN_ROTARY_DATA GPIO_NUM_47
#define PIN_ROTARY_CLK GPIO_NUM_48
#define PIN_ROTARY_SW GPIO_NUM_21

#define PIN_TFT_MISO GPIO_NUM_9
#define PIN_TFT_SCK GPIO_NUM_10
#define PIN_TFT_MOSI GPIO_NUM_11
#define PIN_TFT_DC GPIO_NUM_12
#define PIN_TFT_RESET GPIO_NUM_13
#define PIN_TFT_CS GPIO_NUM_14

#endif

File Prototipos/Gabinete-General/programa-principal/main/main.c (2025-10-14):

#include "esp_log.h"
#include "module_manager.h"
#include "ui_config.h"

static const char* TAG = "Main";

void app_main(void)
{
    ESP_LOGI(TAG, "Starting programa-principal...");
    
    setup_user_interface(); // Initialize user interface
    // Initialize module manager (this will also initialize module connection)
    module_manager_init();
    
    ESP_LOGI(TAG, "Application initialized successfully");
    
    // app_main() can return - other tasks will continue running
    // The module_manager and module_connection tasks handle everything from here
}

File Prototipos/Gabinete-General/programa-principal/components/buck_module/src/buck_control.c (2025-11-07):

/**
 * @file main.c
 * @author your name (you@domain.com)
 * @brief This project is a test for SPI display programming using LVGL library.
 * @version 0.8
 * @date 2025-09-08
 * 
 * @copyright Copyright (c) 2025
 * 
 */

#include "buck_control.h"
#include "buck_interface.h"

#include "gpio_definition.h"
#include <math.h>
#include <sys/lock.h>
#include "esp_log.h"
#include "buck_ui.h"

// FREERTOS
#include "freertos/FreeRTOS.h"
#include "freertos/task.h"
#include "freertos/semphr.h"

// TIMER
#include "driver/gptimer.h"

// GPIO
#include "driver/gpio.h"

// ADC
#include "esp_adc/adc_oneshot.h"
#include "esp_adc/adc_cali.h"
#include "esp_adc/adc_cali_scheme.h"

// LEDC
#include "driver/ledc.h"

// External mutex for LVGL API calls - defined in ui_config.c
extern _lock_t lvgl_api_lock;

// Pin
#define PIN_RELAY PIN_S8 // Pin to control the relay for load switching
#define ADC_MODULE_BUCK_UNIT ADC_S9_UNIT
#define ADC_MODULE_BUCK_CHANNEL ADC_S9_CHANNEL
#define LEDC_MODULE_BUCK_CHANNEL LEDC_CHANNEL_0
#define LEDC_MODULE_BUCK_TIMER LEDC_TIMER_0
#define LEDC_MODULE_BUCK_PIN PIN_S7
#define BUCK_DEFAULT_LOAD BUCK_LOAD_RESISTIVE

// Module identification voltage range (in millivolts)
#define BUCK_IDENT_MV_MIN 1900
#define BUCK_IDENT_MV_MAX 2000

/*----------- CONTROL DEFINES ------------*/
#define DEFAULT_PWM_FREQUENCY 19000 // Frequency of PWM signal.
#define TIMER_PERIOD_US 1000 // Timer period in microseconds, (Ts). 1ms = 1kHz control loop
#define PRINT_LOGS 0 // Set to 1 to print logs, 0 to disable.
#define MAX_PWM_DUTY_CYCLE 4095.0 // Maximum duty cycle for the PWM signal (12-bit resolution)4095.
//#define MAX_PWM_DUTY_CYCLE_11_BIT 2047.0 // Maximum duty cycle for the PWM signal (11-bit resolution).
#define MAX_OUTPUT_VOLTAGE 12.0 // Maximum output voltage of the buck converter in volts.
/*----------------------------------------*/

/*------------ HANDLES -----------*/

static adc_oneshot_unit_handle_t adc1_unit_handle = NULL;   // ADC handle. Used to save the ADC configurations.
static adc_cali_handle_t adc1_cali_handle = NULL;  // ADC calibration handle.
static gptimer_handle_t gptimer_handle = NULL; // Timer handle used for PID control and to make the sampling time consistent.
static TaskHandle_t xTaskControlUpdate_handle = NULL; // PID task handle. Used to notify the PID task when the timer is triggered.
static TaskHandle_t xTaskUIUpdate_handle = NULL; // UI update task handle for cached values
static TaskHandle_t xTaskLoadUpdate_handle = NULL; // Load type update task handle
static SemaphoreHandle_t xControlModeMutex = NULL; // Mutex to protect access to the control mode variable.
static SemaphoreHandle_t xLoadTypeMutex = NULL; // Mutex to protect access to the load type variable.

// Shutdown flags for graceful task termination
static volatile bool shutdown_pid_task = false;
static volatile bool shutdown_ui_task = false;

// Cached UI values to avoid blocking PID loop
static volatile uint32_t cached_fixed_pwm_value = 0;
static volatile uint32_t cached_setpoint_v = 0;
static volatile uint32_t cached_pwm_frequency = DEFAULT_PWM_FREQUENCY;

/*--------------------------------*/

const char* MODULE_TAG = "Buck Control"; // Module name for logging


volatile control_mode_t control_mode = CONTROL_MODE_IDLE;
static buck_load_type_t buck_load_type = BUCK_DEFAULT_LOAD;
/*-------------------------------------------*/

//PID variables
// PID constants and variables
const float Kp = 0.5;
const float Ki = 65.0;
const float Kd = 0;
const float Ts = TIMER_PERIOD_US / 1000000.0;
const float Nc = 3;

// PID coefficients. These coefficients are obtained from the PID with derivative filter
const float a_coefficients[3] = {
    1,
    -2 + Nc * Ts,
    1 - Nc * Ts
};
const float b_coefficients[3] = {
    Kp + Kd * Nc,
    -2 * Kp - 2 * Kd * Nc + Ki * Ts + Kp * Nc * Ts,
    Kp + Kd * Nc - Ki * Ts - Kp * Nc * Ts + Ki * Nc * Ts * Ts
};
/*------------------------------------------*/

/*-------- FUNCTION PROTOTYPES --------*/
void start_buck_module(void); // Function to start the buck converter module
void stop_buck_module(void); // Function to stop the buck converter module
void set_control_mode(control_mode_t new_mode); // Function to set the control mode
control_mode_t get_control_mode(void); // Function to get the current control mode
static void delete_gpio(void); // Function to delete the GPIO
static void delete_adc(void); // Function to delete the ADC
static void delete_timer(void); // Function to delete the timer
static void delete_ledc(void); // Function to delete the LEDC
static void create_module_tasks(void); // Function to create the PID task
static void delete_module_tasks(void); // Function to delete the PID task

static void adc_init_and_config(void); // ADC initialization and configuration
static void adc_cali_config(void); // ADC calibration configuration
static void ledc_config(void); // LEDC configuration
static void gptimer_config(void);  // Timer configuration
static void configure_gpio(void); // GPIO configuration
static bool gptimer_on_alarm_callback(gptimer_handle_t timer, const gptimer_alarm_event_data_t *edata, void *arg);  // Timer callback function
long map(long x, long in_min, long in_max, long out_min, long out_max); 
/*-------------------------------------*/

/*------- TASKS FUNCTION PROTOTYPES -------*/
static void vTaskUIUpdate(void *arg); // UI update task function to cache values
static void vTaskControlUpdate(void *arg); // PID task function
static void vTaskLoadUpdate(void *arg); // Load type update task function
/*----------------------------------------*/

/* ----------- MODULE DECLARATION ----------- */
const module_t buck_module = {
    .name = "Buck Converter Module",
    .ident_mv_min = BUCK_IDENT_MV_MIN,
    .ident_mv_max = BUCK_IDENT_MV_MAX,
    .start_function = start_buck_module,
    .stop_function = stop_buck_module,
};
//

void start_buck_module(void){
    // Initialize shutdown flags
    shutdown_pid_task = false;
    shutdown_ui_task = false;
    
    start_buck_interface();

    adc_init_and_config();
    adc_cali_config();
    ledc_config();
    configure_gpio();
    create_module_tasks();
    gptimer_config();    
}

void stop_buck_module(void){
    // Stop timer BEFORE deleting tasks (important order)
    delete_timer();

    // Now safe to delete tasks
    delete_module_tasks();
    
    // Clean up hardware
    delete_adc();
    delete_ledc();
    delete_gpio();

    ESP_LOGI(MODULE_TAG, "Before stop buck interface.");
    stop_buck_interface();
    ESP_LOGI(MODULE_TAG, "After stop buck interface.");
}   

// Function to safely set control mode
void set_control_mode(control_mode_t new_mode) {
    if (xControlModeMutex != NULL && xSemaphoreTake(xControlModeMutex, pdMS_TO_TICKS(100)) == pdTRUE) {
        control_mode = new_mode;
        xSemaphoreGive(xControlModeMutex);
    } else {
        ESP_LOGE(MODULE_TAG, "Failed to get control mode mutex");
        control_mode = CONTROL_MODE_FAULT;
    }
}
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

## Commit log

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2025-02-25 Primeros avances prototipo dimmer
    [BT137-600E,127.stp, ProtDimmer.kicad_pcb, ProtDimmer.kicad_sch]
2025-02-25 Primeros avances en prototipo de convertidor Buck
    [IRF9540NPBF.step, buck_converter.kicad_pcb, buck_converter.kicad_sch]
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2025-03-06 Avances circuito KiCad, nuevos calculos para frecuencia más baja
    [buck_converter.kicad_sch]
2025-03-10 Avances diseño del circuito, definición de algunos componentes
    [buck_converter.kicad_sch]
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2025-03-10 Cambio de valores en circuito
    [buck_converter.kicad_sch]
2025-03-10 Primeros ajustes para adaptar a 48 Vac
    [ProtDimmer.kicad_sch]
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2025-03-12 Diseño del circuito final, agregado de nuevas librerías
    [IRLML6344.step, buck_converter.kicad_sch]
2025-03-12 Corrección de valor Rg
    [buck_converter.kicad_sch]
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2025-03-13 Agregado red snubber driver
    [buck_converter.kicad_sch]
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2025-03-19 Agregar valores componentes, eliminar contenido de otras tareas
    [ProtDimmer.kicad_sch]
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2025-03-19 Agregar diseño Inversor con IC555
    [Half Bridge Inverter.kicad_pcb, Half Bridge Inverter.kicad_sch]
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2025-03-21 Agregado de diseño de disparo con BJT
    [buck_converter.kicad_sch]
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2025-03-21 Arreglo de tabla E/S
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2025-03-24 Modificar nombres carpetas, dejar todas las librerias sueltas
    [BT137-600E,127.stp, IRF9540NPBF.step, IRLML6344.step]
2025-03-25 Primeros avances con PCB de Buck
    [buck_converter.kicad_pcb, buck_converter.kicad_sch]
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2025-03-26 Avances en PCB convertidor buck
    [buck_converter.kicad_pcb, buck_converter.kicad_sch]
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2025-03-26 Agregar librerias, asignar footprints, comenzar pcb
    [MOC3021.STEP, MOC3021.step, ProtDimmer.kicad_pcb]
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2025-03-26 Agregar cambios en esquema
    [Half Bridge Inverter.kicad_pcb, Half Bridge Inverter.kicad_sch]
2025-03-27 Agregado archivo KiCad Convertidro Boost
    [boost_converter.kicad_pcb, boost_converter.kicad_sch]
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2025-04-01 Modificar footprint relé, arreglar conexión faltante
    [ProtDimmer.kicad_pcb]
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2025-04-01 Agregado de driver de mosfet
    [boost_converter.kicad_sch]
2025-04-01 Diseño de circuito sin valores
    [boost_converter.kicad_sch]
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2025-04-03 Arreglar texto pcb y agregar letras y números guía
    [ProtDimmer.kicad_pcb]
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2025-04-04 Revert a 94adb22813541da8d2dbf94c6875279e77480e3e otra vez
    [Half Bridge Inverter.kicad_pcb, Half Bridge Inverter.kicad_sch]
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2025-04-17 Corrección PCB Buck, para disminuir tamaño
    [buck_converter.kicad_pcb, buck_converter.kicad_sch]
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2025-05-20 Inicio de PCB final Buck
    [buck_converter_final.kicad_pcb, buck_converter_final.kicad_sch, inductor_toroidal.stp]
2025-05-21 Primera versión PCB final Buck
    [buck_converter_final.kicad_pcb, buck_converter_final.kicad_sch]
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2025-05-27 Add volatile flag, fix ISR logging, change map function name
    [main.c]
2025-05-27 Add defines for alarm values, correct spelling error, remove floating-point operation in map function
    [main.c]
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2025-05-28 Fix .step path, add scale factor,correct spelling
    [main.c]
2025-05-28 Add readme, correct spelling error
    [main.c]
2025-05-30 Avances PCB convertidor Buck
    [buck_converter_final.kicad_pcb, buck_converter_final.kicad_sch]
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2025-06-02 Avances en PCB final buck, versión 1.1
    [buck_converter_final.kicad_pcb, buck_converter_final.kicad_sch]
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2025-06-04 Agregar diseño 3D Gabinete Chico
    [Gabinete Chico 0.1.FCStd, Gabinete Chico 0.2.FCStd, Gabinete Chico 0.3.FCStd]
2025-06-04 Agregar diseños 3D gabinete grande
    [Gabine Grande Base.FCStd, Gabine Grande Superficie.FCStd]
2025-06-04 Organizar kicad dimmer y agregar versión inicial final
    [Dimmer_final.kicad_pcb, Dimmer_final.kicad_sch, ProtDimmer.kicad_pcb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]
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2025-06-04 Agregar archivos 3d gabinete chico
    [Gabinete Chico 0.2.1.FCStd, GabineteChicov2-1.stl, Suplemento.FCStd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]
2025-06-04 Agregar modificaciones diseños 3D
    [Gabinete Chico 0.2.1.FCStd, Gabinete Chico 0.2.2.FCStd, GabineteChicov2-2.stl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]
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2025-06-06 Conectar símbolo PCIe x4, agregar identificación
    [Dimmer_final.kicad_sch]
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2025-06-19 Agregar M4s a la derecha y retoques generales
    [Dimmer_final.kicad_pcb]
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2025-06-30 Cambiar file path del modelo 3d del optotriac por uno relativo
    [Dimmer_final.kicad_pcb]
2025-06-30 Cambiar file path del modelo 3d del pote por uno relativo
    [PCB Final Inversor 555.kicad_pcb]
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2025-07-15 Corregir errores y warnings
    [PCB Final Inversor 555.kicad_pcb]
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2025-07-25 Agregar redacción disipación de potencia, arreglo en cálculos
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2025-07-30 Arreglar unidades, cross-references y agregado de algunas citas bibliograficas
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2025-08-03 Modificaciones en soporte de pantalla
    Se saca del modelo superior del gabinete general. Se diseña como una pieza aparte.
    [Angulo Pantalla.FCStd, Gabine Grande Superficie 2.0.FCStd]
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2025-08-05 Agregar diseño inicial PCB general, símbolo ESPs y display
    [PCB-general.kicad_pcb, PCB-general.kicad_sch]
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2025-08-13 Modificaciones en gabinete chico
    Modificaciones en medidas de ventana para conector.
    Redondeo de esquinas R5mm
    [Gabinete Chico 2.0.FCStd, Gabinete _Chico_Final.stl]
2025-08-13 Carcasa y tapa para conector
    55x25 y 50x20
    [Carcasa.FCStd, Tapa carcasa.FCStd]
2025-08-14 Arreglar ortografía y mejorar claridad informe Buck
2025-08-14 Agregar nombre a diodos, cambiar UC por uC
    [Dimmer_final.kicad_sch]
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2025-08-18 Revert "Merge - Carcasa y tapa para conector"
    [Carcasa.FCStd, Tapa carcasa.FCStd]
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2025-08-25 Modificaciones en carcasa y tapa. Tamaños y redondeo de esquinas
    [Carcasa.FCStd, Tapa carcasa.FCStd]
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2025-09-08 Terminaciones en parte superior de gabinete general y ángulo para pantalla.
    [Angulo Pantalla.FCStd, Angulo.stl, Gabine Grande Superficie 2.0.FCStd]
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2025-09-18 Reversionado dimmer para fabricación industrial
    [Dimmer_final.kicad_pcb, Dimmer_final.kicad_sch]
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2025-09-18 Modificaciones en esquemático y PCB inversor medio puente.
    [PCB Final Inversor 555.kicad_pcb, PCB Final Inversor 555.kicad_sch]
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2025-09-23 Añadir punto de prueba y actualizar valor de resistencia R1 a 33k
    [Dimmer_final_alt.kicad_sch]
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2025-09-25 Modificación de ángulo para pantalla y limpieza de archivos basura.
    [Angulo Pantalla.FCStd, Angulo.stl, Gabine Grande Base 2.0.FCStd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]
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2025-09-26 Cambiar de lugar gabinete-general y arreglar pines
    [PCB-general.kicad_pcb, PCB-general.kicad_sch]
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2025-10-08 Fix stop_buck_module and ui deletion.
    [buck_control.c, ui_config.c]
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2025-10-08 Add UI update task and caching mechanism to improve performance and prevent blocking in the Buck control
    [buck_control.c]
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2025-10-10 Add idle screen and fix memory leak in each UI
    [ui_config.c]
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2025-10-22 Mejorar module connection y module manager para evitar crasheos. Migrar a versión 5.5.1 de esp-idf
    [module_manager.c]
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2025-10-28 Corregir bug desconexión dimmer
    [dimmer_control.c]
2025-10-28 Aumentar stack size y corregir bug dimmer
    [dimmer_control.c]
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2025-10-29 Remover licencia para solucionar bug
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2025-10-30 Agregar resultados dimmer. Corregir resultados inversor. Corregir resultados buck y agregar comentarios a resolver del mismo.
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2025-11-04 Corregir bugs buck
2025-11-04 Comentar logs para evitar crasheos
    [module_manager.c]

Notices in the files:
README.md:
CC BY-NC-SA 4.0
